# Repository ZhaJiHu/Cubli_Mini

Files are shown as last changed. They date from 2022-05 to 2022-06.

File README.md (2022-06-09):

# Cubli_Mini项目

本项目ID是来源于苏黎世联邦理工学院的Cubli，电机驱动使用的是Simple FOC。低成本、小型化、简化后作为我的首个开源项目

**项目完全开源，任何人都可以根据本Github内容自行白嫖，当然也可以顺手点个Star**

### 介绍

本项目在原版Cubli的基础上去掉主动刹车，缩小体积和一定的简化。需要手动调整到平衡点附近，才可以实现边和点平衡。Cubli_Mini是一个10x10x10CM的立方体，集电机驱动、充放电一体化。满电状态下，点平衡在无扰动下续航≥5小时。

项目成本：≤800RMB

**视频介绍：**[https://www.bilibili.com/video/BV1UR4y1c74B?spm_id_from=333.999.0.0](https://www.bilibili.com/video/BV1UR4y1c74B?spm_id_from=333.999.0.0)

YouTube：[https://youtu.be/JwiJBd6I_vY](https://youtu.be/JwiJBd6I_vY)

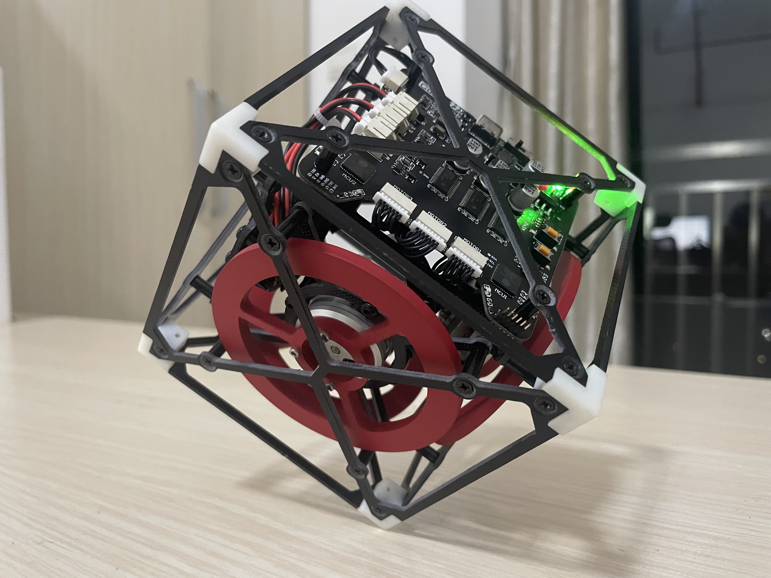
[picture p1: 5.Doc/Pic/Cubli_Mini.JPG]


### 资料更新说明（2022/6/7）

- **修复**：修复PCB BOM表采购链接的部分链接错误问题，**一共有4处，已经红色标红**。已经下单的同学需要自己校验看元器件是否是正确
- **增加**：PCB BOM表采购链接里的**贴片按键增加备用链接**

### 资料更新说明（2022/5/22）

- PCB BOM表添加采购链接
- 更新<写给小白的白嫖教程.pdf><代码和工程>，图文并茂说明如何解决头文件错误问题

### 资料更新说明（2022/5/21）c23

- /6.Process/钣金件/，增加对应的step文件
- /6.Process/3D打印/，增加对应的step文件
- **安全说明**
  - **动量轮比较危险，要注意安全，手远离动量轮**
  - /2.Firmware/MCU1/control/cubli_mini.h，修改VOLTAGE_LIMIT的电压可以限制飞轮的最大输出，开始使用建议降低该参数，可以从4，5V开始

### 资料更新说明（2022/5/19)

- 最新发现动量轮有两个角忘了倒角了，理论上会影响大转速下的动平衡，因此对此进行修改。已经下单打样的同学也可以正常使用，因为电机KV值很低，我现在使用的也是漏倒角的动量轮。更新了/4.Model/Cubli_Mini.STEP文件。并且更新了/6.Process/钣金件/YC.JGJ.000002.4.*，文件版本号更新到.4
- 还有说一下结构件的采购数量和采购链接都在/6.Process/BOM/结构BOM.xls
- 物料采购的时候注意编码器模块需要3套物料

### 资料说明

- 3D模型设计源文件
- 主控模块、IMU模块、编码器模块、下载模块硬件工程
- 主控1、主控2软件工程
    - 主控模块使用两颗ESP32
- 网络调试助手
    - WIFI调参使用
- 各类文档说明
    - 对项目的一些说明，如调参，按键操作，控制原理等
- 打样文件
    - STL格式3D打印文件
    - DWG格式钣金文件
    - BOM表
        - 结构BOM表
        - PCB元器件BOM表

### 结构设计

由于我只学了一周的SW，因此有些零件会漏画一些内容，如螺丝螺纹，铜柱内螺纹啥的

外框等钣金件采用的是成本较低的玻纤板，在保证刚性的情况下降低成本。动量轮采用的是304不锈钢，可以在小体积下提供较大的转动惯量。辅以少量3D打印件组成。连接件为了美观使用的是阳极氧化铝柱，当然也可以自行使用成本更低的铜柱。整体结构件成本为350块以内，铝柱更换铜柱可以降低到290以内

**注意事项：**

- Cubli_Mini的八个角点，是由两种不同的角组成，名字为角1和角2，各4个
- 外框和角的连接处的结构不是45°对称，所以是有安装方向的，详情看DoC/结构和安装说明

### 电路模块

**主控模块：**

- 主控模块集成了3个电机驱动电路，电池充放电路，降压稳压电路，CAN通讯电路
- 由于单颗ESP32只有6路电机PWM，因此使用了两颗ESP32模块，使用了CAN作为MCU间的通讯方式，由于两颗ESP32都是集成在同一个主板上，因此为了节省IC成本，可以把CAN修改为IIC，UART，SPI等各类短路径通讯方式，但是需要修改主控软硬件，有想法的同学可以自行修改
- 电机驱动电路参考Simple FOC开源电路，Simple FOC链接：[https://github.com/simplefoc](https://github.com/simplefoc)。电池充放电参考：[https://oshwhub.com/qqj1228/zi-ping-heng-di-lai-luo-san-jiao_10-10-ban-ben](https://oshwhub.com/muyan2020/zi-ping-heng-di-lai-luo-san-jiao_10-10-ban-ben_copy)

**IMU模块：**

- 使用最为常见的MPU6050
- 为了防止应力，对IMU所在区域挖槽，减少安装应力。但使用了3颗螺丝硬连接，并不能避免应力问题，改进方案为使用软垫片并只拧紧一个螺丝进一步减少应力
- 由于IMU安装要求比较高，因此在贴片时，尽量保证MPU6050与PCB平行，且位于焊盘正中央

**编码器模块：**

- 采用的是成本较低的AS5600，在低速情况下便宜好用

**自动下载模块：**

- 为了尽量减少主控的面积，因此单独把自动下载电路摘出来，参考官方自动下载电路

**注意事项：**

- 正常情况下，自动下载模块焊接排针，主控不焊接任何排针/排母

### 固件说明

Cubli_Mini的核心内容为Simple FOC电机驱动库以及点平衡控制算法，运行在MCU1中。MCU2只是使用了Simple FOC库对电机2和电机3的控制，利用CAN反馈和接收控制命令。

**MCU1固件说明：**

- bsp：基于arduino库封装了一下LED，KEY，ADC，非易失储存等内容
- comm：公用类，目前只封装了一个时间类，获取时间差，非延时等待等简单内容
- control：核心库，内容为平衡算法和调参接口，调参参考Simple FOC格式。为方便使用，使用的是字符串，不使用传统的16进制协议
- main：main文件，驱动的初始化和FreeRTOS任务创建
    - ESP32官方把WIFI，蓝牙类运行在Core0。因此在创建任务中，把WIFI任务创建在Core0中，其他则创建在Core1。只有运行于不同核心任务的数据交互我才加了互斥锁。

**注意事项：**

- 目前WIFI SSID和PSW，TCP Server IP Port全部是写死在固件里面，因此要想使用WIFI调参需要修改这些内容，详情请看Doc/使用和调参说明

### 打样说明

考虑到很多同学可能是第一次进行结构打样，因此提供了打样文件

**3D打印：**

- 文件位于：/6.Process/**3D打印**，该文件为STL格式，打样数量请查看同目录下的<**3D打印加工说明**>，可以在未来工厂或者嘉立创打样，首选光固化
- 文件名称使用的是料号，料号方便管理，尾号没有.X都代表为第一版

**钣金件打样：**

- 文件位于：/6.Process/**钣金件**，**每个物料的都有对应的PDF和DWG文件，PDF文件方便查看，DWG文件用于激光切割/板材加工**。打样数量请查看同目录下的<**钣金加工说明**>，可以找淘宝给图纸直接加工。由于加工精度要求不高，个人用途下，公差全看加工厂的心情
- 也可以直接找到对应的step文件给淘宝加工

**PCB打样：**

- 从硬件工程拿着PCB文件出门左转嘉立创白嫖

**BOM表：**

- 文件位于：/6.Process/**BOM**
- 结构BOM表，里面列有需要购买的**结构物料和链接**
- PCB BOM表，里面列有需要购买的元器件物料，也可以自行找到AD工程导出
- **注意事项：**
    - PCB BOM表是从AD源文件导出，工程会有重复用料，需要注意
    - **注意编码器需要3块，需要采购3套物料**
    - DRV8313、ESP32、AS5600、IMU可以去淘宝购买，其他右转立创商城BOM表下单。
    - **注意贴片型铝电解电容的封装，主控板有限高区域，限高高度为8mm**
    - 如文件有遗漏的地方望提醒

**写给小白的白嫖教程：**

- 文件位于：/Doc/写给小白的白嫖教程.pdf，手把手教你如何完成本项目的白嫖

### 控制算法

Cubli_Mini使用的是LQR来进行控制，也可以使用串级PID来进行控制。代码位于/需要修改/MCU1/control/cubli_mini

**边平衡**：

- 可以参考一阶倒立摆进行建模和求解参数。由于建立模型的参数比较难准确的获得，我求解得到的参数和最佳参数有些许出入。因此本项目大多数使用玄学调参工程师来整定参数

**点平衡：**

- 在边平衡的基础上添加对X，Z轴的控制。采用与边平衡一样的控制方法，详情看Doc/控制原理说明。

**研究型：**

- 请查看原版Cubli的论文

### 调参

**调节方法：**

- 可以使用UART和WIFI进行调参，WIFI需要连接到路由器，Cubli_Mini为TCP客户端

**调节命令：**

- 详情命令请查看Doc/调参命令说明

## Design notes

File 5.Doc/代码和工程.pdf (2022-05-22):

# 代码和⼯程

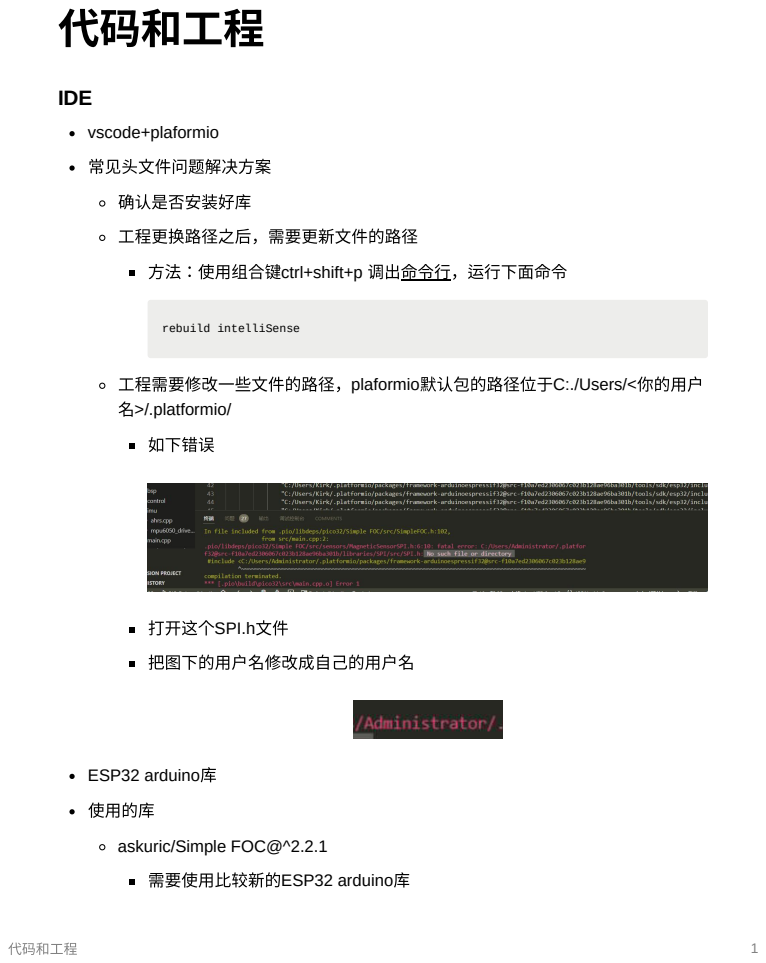
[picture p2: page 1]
代码和⼯程; IDE; vscode+plaformio; 常⻅头⽂件问题解决⽅案; 确认是否安装好库; rebuild intelliSense; 如下错误; 打开这个SPI.h⽂件; ESP32 arduino库

⼯程更换路径之后，需要更新⽂件的路径

⽅法：使⽤组合键ctrl+shift+p 调出命令⾏，运⾏下⾯命令 (https://so.csdn.net/so/search?q=%E5%91%BD%E4%BB%A4%E8%A1%8C&spm=1001.2101.3001.7020)

⼯程需要修改⼀些⽂件的路径，plaformio默认包的路径位于C:./Users/<你的⽤户
名>/.platformio/

把图下的⽤户名修改成⾃⼰的⽤户名

askuric/Simple FOC@^2.2.1
需要使⽤⽐较新的ESP32 arduino库

分⽀号为：6cfe4613e4b4846e1ab08c7f78b7ea241f52c7da

请查看⼯程⽬录下的plaformio.ini⽂件

miwagner/ESP32CAN@^0.0.1

### MCU1⽬录树

Mcu1
├─ .gitignore
├─ .vscode
│ ├─ extensions.json
│ └─ settings.json
├─ include
│ ├─ bsp 基于arduino库封装了⼀下
│ │ ├─ adc.h
│ │ ├─ bsp_driver.h
│ │ ├─ can.h
│ │ ├─ key.h
│ │ ├─ led.h
│ │ └─ my_eeprom.h
│ ├─ comm 公共类
│ │ └─ time.h
│ ├─ config 配置⽂件
│ │ └─ config.h
│ ├─ control 核⼼库，控制和调参
│ │ ├─ cubli_mini.h
│ │ ├─ param.h
│ │ ├─ serial_commander.h
│ │ └─ wifi_commander.h
│ ├─ imu IMU驱动和融合
│ │ ├─ ahrs.h
│ │ └─ mpu6050_driver.h
│ └─ README
├─ lib
│ └─ README
├─ platformio.ini
├─ README.md

├─ src
│ ├─ bsp
│ │ ├─ can.cpp
│ │ ├─ key.cpp
│ │ ├─ led.cpp
│ │ └─ my_eeprom.cpp
│ ├─ control
│ │ ├─ cubli_mini.cpp
│ │ ├─ param.cpp
│ │ ├─ serial_commander.cpp │ │ └─ wifi_commander.cpp
│ ├─ imu
│ │ ├─ ahrs.cpp
│ │ └─ mpu6050_driver.cpp
│ ├─ main.cpp
│ └─ workspace.code-workspace └─ test
└─ README

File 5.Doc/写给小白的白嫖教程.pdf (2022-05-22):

写给⼩⽩的⽩嫖教程 | 1

# 写给⼩⽩的⽩嫖教程

下载

1. clone或者Download整个项⽬

下单

1. PCB打样
a. 进⼊\1.Hardware\
b. 找到每⼀个硬件⼯程的PCB⽂件，直接右转丢到嘉⽴创打样
2. 开钢⽹
a. 把4个⼯程的PCB⽂件⼀起丢给淘宝，让淘宝开⼀张钢⽹就⾏
3. 下单3D打印件
a. 进⼊\6.Process\3D打印
b. 按照<3D打印加⼯说明.xlsx>⽂档说明，看清楚数量，去未来⼯⼚把3个物料丢上 去打印，材料选未来8100
4. 下单钣⾦件
a. 进⼊\6.Process\钣⾦件
b. 按照<钣⾦加⼯说明.xlsx>⽂档说明，看清楚数量，⾃⼰去淘宝打样或者找到 \6.Process\BOM\结构BOM.xls⽂件，点进去⽂件的链接，丢⽂件给客服，确定好 数量开⼯
5. 下单结构件
a. 进⼊\6.Process\BOM\
b. 按照<结构BOM.xls>下单除开钣⾦件的其他材料
6. 下单元器件
a. 进⼊进⼊\6.Process\BOM\
b. 按照<AS5600.xlsx><Cubli_Control_Board.xlsx><ESP32_UART.xlsx> <mpu6050.xlsx>⽂档下单元器件 i. 嫌⿇烦，有钞能⼒的除开AS5600去淘宝，其他全去⽴创商城BOM表下单， 需要注意贴⽚型铝电解电容的封装，主控板有限⾼区域，限⾼⾼度为8mm

ii. 淘宝IC⽔深，注意别翻⻋了

iii. 贴出了元器件链接

### 安装IDE和编译

1. 等物料的过程可以在PC装好Vscode+plaformio环境
a. 请去百度或者B站搜索相关教程
2. 编译\2.Firmware⾥MCU1、MCU2的代码，编译有些问题可以查看\5.Doc\代码和⼯ 程.pdf，有其他问题可以百度解决

## PCB焊接

1. 先焊接PCB
a. 可以看看视频⽅法，没有加热台⽤热⻛枪吹
b. 注意：要注意IMU模块的⽴贴接插件，引脚是否焊接到PCB上，这⾥经常翻⻋
2. 焊接完PCB⼀定要测试⼀下
a. 把所有的模块接上线
b. ⽤万⽤表打到⼆极管档位或者通断档位
c. 分别测量VBUS\BAT+\12V\5V\3.3V与GND的测试点，看是否有短路，⽆异常就 可以了
3. 把电机和编码器部分先装配好
a. 作⽤：为了测试功能
4. 上电测试主控、IMU、电机、下载模块
a. 线都接好了，就可以上电了下载代码了，给2个MCU都下载代码，注意MCU编 号，⽤串⼝助⼿查看是否所有模块都正常初始化？
b. 电池⼀定要注意线序
c. 初始化通过后，按3次KEY2切换到电机测试模式，⻓按KEY1，正常的话3个电机 都能正常运⾏。模式和状态指⽰灯请查看<模式以及切换（KEY）说明.pdf><LED 指⽰灯说明.pdf>

装配

1. 确保硬件都没问题了，就可以开始装配了，装配没啥难度，按照\4.Model\⾥⾯的⽂件 或者视频装配就可以了，就是需要注意⼀下
a. ⾓和外框装配有⽅向，可以看<结构和安装说明>
b. 电机CH1、CH2、CH3也按照<结构和安装说明>来接线
2. 都装配完成就可以开始正常上机了
a. 按⼀次KEY2切换到点平衡模式，绿⾊LED3S内闪烁⼀次
b. ⼿动把Cubli_Mini⽴起来放到平衡点附近，静⽌0.5S就可以正常运⾏了，本步骤 只是确保系统和传感器都能正常运⾏
c. 未调整平衡⾓度有⼀定的概率能⽴起来
d. 注意事项
i. ⼀定⼀定要注意安全，⼿要远离动量轮

ii. ⼀开始⼀定要调低输出的电压阈值，调整⽅法
为：/2.Firmware/MCU1/control/cubli_mini.h，修改VOLTAGE_LIMIT的电压 可以限制⻜轮的最⼤输出，开始使⽤建议降低该参数，可以从4，5V开始

调参

1. 按照<使⽤和调参说明.pdf>使⽤串⼝或者WIFI调参
2. 按照<常⻅问题.pdf>第五点调节平衡⾓度，调节的命令查看<调参命令说明.pdf>

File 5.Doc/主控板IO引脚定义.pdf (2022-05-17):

主控板IO引脚定义 | 1

# 主控板IO引脚定义

# MCU1

类型 | 作⽤ | 引脚定义
MOTOR1 | PWM1 | IO25
| PWM2 | IO26
| PWM3 | IO27
| PWM_EN | IO33
| SCL | IO14
| SDA | IO4
CAN1 | CAN_TXD | IO15
| CAN_RXD | IO13
LED | LED_BLUE | IO10
| LED_GREEN | IO9
| LED_MOTOR_GREEN | IO21
ADC | BAT_V | IO36
IMU | SCL | IO18
| SDA | IO5
| INTERRUPT | IO23
KEY | KEY1 | IO22
| KEY2 | IO19

# MCU2

类型 | 作⽤ | 引脚定义
MOTOR2 | PWM1 | IO25
| PWM2 | IO26
| PWM3 | IO27
| PWM_EN | IO33

主控板IO引脚定义 | 2
类型 | 作⽤ | 引脚定义
| SCL | IO14
| SDA | IO4
MOTOR3 | PWM1 | IO22
| PWM2 | IO19
| PWM3 | IO23
| PWM_EN | IO21
| SCL | IO18
| SDA | IO5
LED | LED_MOTOR_GREEN | IO10
CAN2 | CAN2_TXD | IO15
| CAN2_RXD | IO13

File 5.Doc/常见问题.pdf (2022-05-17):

常⻅问题 | 1

# 常⻅问题

1. 为什么系统上电初始化需要静置?
a. 原因：IMU零偏问题，IMU需要连续1.5S的时间采集陀螺仪的数据做为零偏，静 置的条件默认需要三轴陀螺仪的读数＜5deg/s（默认，可以在 include/config/config.h中修改阈值），如果IMU的零偏值过⼤，建议更换零偏值 较⼩的IMU
2. 为什么我的IMU模块零偏特别⼤？
a. 安装应⼒，虽然IMU模块把IMU单独挖出来，但是因为上了3颗螺丝，IMU仍然有 可能会受到应⼒的变化，这时候可以通过添加软垫⽚的⽅法解决⼀部分，螺丝尽 量别打太紧，把IMU固定即可
b. IMU IC（mpu6050）原因，IC由于是mems传感器，可能会由于跌落等原因导致 IMU的物理结构受到影响，因⽽导致零偏过⼤，零偏过⼤，不建议使⽤
3. 为什么每个cubli都需要校准平衡的⾓度偏差值？
a. IMU安装之后的轴偏差问题，只讨论轴的所在平⾯是否垂直，不讨论原点是否重 合平⾯的问题
i. 单边平衡问题，结构设计上，处于平衡状态时，IMU反馈的⾓度理论上应该 为0。但是由于⽀点也好，IMU安装件也好都由于误差，会导致在平衡状态 时，IMU的读数不为0，因此需要校准⾓度偏差值

ii. 单点平衡问题同理

4. 为什么我明明已经调参到最佳平衡点了，每次重新上电后总是会发⽣变化，系统不处 于我上次调整的状态？
a. IMU的零偏问题，由于每次IMU上电后零偏会发⽣变化，带来的是融合结果发⽣ 变化，因此体现在动态⾓度上会有些许变化，导致平衡点产⽣偏移，因此上次校 准值不再为最佳参数
b. 解决⽅法
i. 更换性能更好的IMU模块

ii. 采⽤性能更好的IMU融合算法

iii. 对IMU的加速度计和陀螺仪都进⾏校准

常⻅问题 | 2
5. 怎么调整平衡点？
a. 单边情况下，观察动量轮的转动⽅向和转动速度，转动⽅向是与⽅块倾斜⽅向⼀ 致，平衡⾓的偏差⼤⼩决定系统需要的转动惯量，如转动⽅向为顺时针，那么⽅ 块⼀定是往右倾斜，因此需要往反⽅向调节平衡⾓度，调整到动量轮速度⼏乎为 0，这时候就为最佳平衡点
b. 单点情况下，X\Y轴哪个轴倾斜⼤调哪个，调节⽅法同单边
6. 为什么按照默认参数不能⽴起来？
a. 在系统中，控制⾓度θ越⼤，需要的转动惯量也就越⼤。想要更⼤的转动惯量， 要么提⾼动量轮的质量，要么提⾼动量轮的转速。因为所⽤的动量轮质量是恒定 的，所以只能提⾼动量轮的转速。由于所选电机的转速较低，因此很容易达到电 机最⼤转速，失去调节效果，所以⽴⽅体就⽆法再保持平衡。因此需要调整theta ⾓，使得⽴⽅体在转速范围内能提供⾜够的转动惯量去维持⽴⽅体的平衡。

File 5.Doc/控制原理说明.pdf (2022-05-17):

# 控制原理说明

## 单边平衡

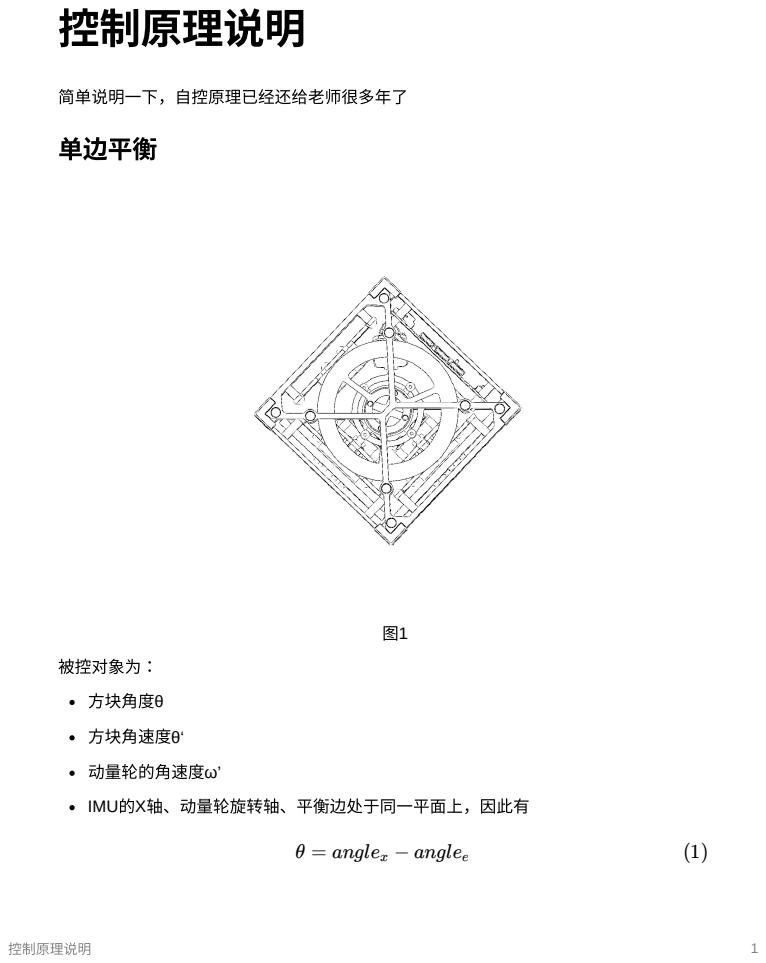
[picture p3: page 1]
控制原理说明; 被控对象为：; ⽅块⾓速度θ‘; 动量轮的⾓速度ω’; θ = anglex − anglee

简单说明⼀下，⾃控原理已经还给⽼师很多年了

IMU的X轴、动量轮旋转轴、平衡边处于同⼀平⾯上，因此有

结合（1）（2）（3）可得

### 参数整定

参数 | 默认数值（默认不 改结构件） | 说明
Kp | -25
Kv | 2
Ks | 0.5
angle_e | 0 | IMU安装误差

## 单点平衡

控制原理为在单边平衡的基础上增加对Y、Z轴的控制

结构如图2所⽰

θ =

′ | gyrox | (2)
ω’ = motorspeedx | (3)
Lqr = (anglex − anglee ) × kp + gyrox × kv + motorspeedx × ks | (4)

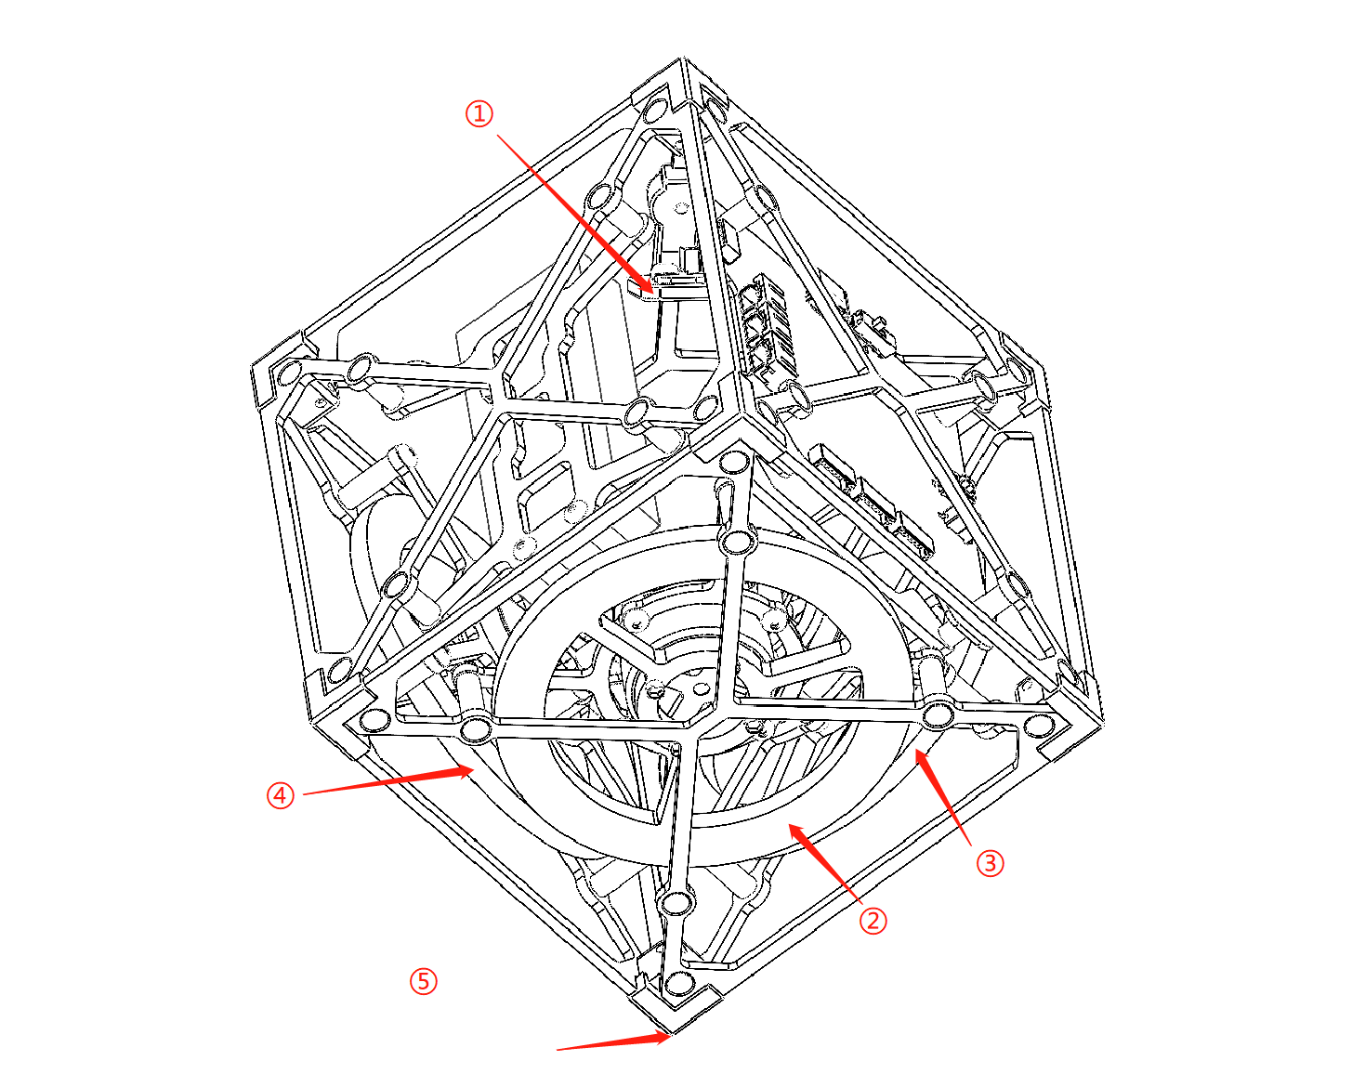
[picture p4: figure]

图2

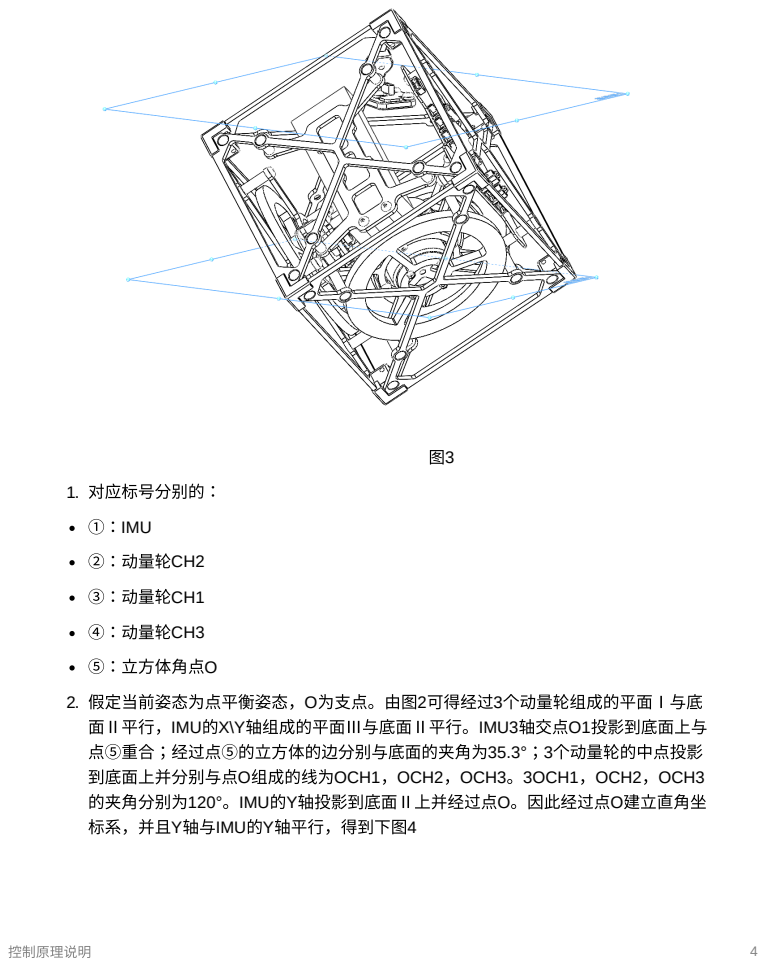
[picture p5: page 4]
1. 对应标号分别的：; ①：IMU; ②：动量轮CH2; ③：动量轮CH1; ④：动量轮CH3

2. 假定当前姿态为点平衡姿态，O为⽀点。由图2可得经过3个动量轮组成的平⾯Ⅰ与底
⾯Ⅱ平⾏，IMU的X\Y轴组成的平⾯Ⅲ与底⾯Ⅱ平⾏。IMU3轴交点O1投影到底⾯上与
点⑤重合；经过点⑤的⽴⽅体的边分别与底⾯的夹⾓为35.3°；3个动量轮的中点投影
到底⾯上并分别与点O组成的线为OCH1，OCH2，OCH3。3OCH1，OCH2，OCH3
的夹⾓分别为120°。IMU的Y轴投影到底⾯Ⅱ上并经过点O。因此经过点O建⽴直⾓坐
标系，并且Y轴与IMU的Y轴平⾏，得到下图4

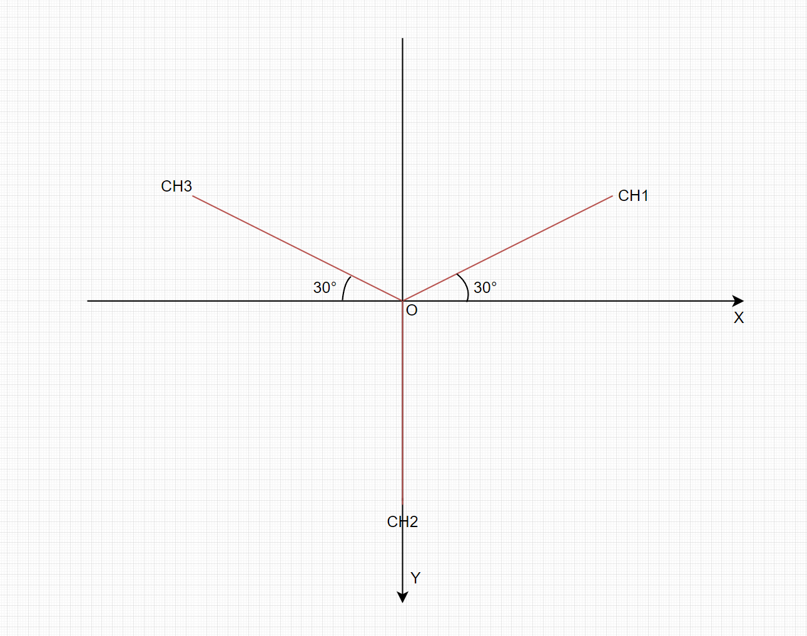
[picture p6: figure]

图4

3. 动量轮CH1\CH2\CH3的转动速度⽅向与OCH1\OCH2\OCH3垂直，因此分别平⾏移 动到经过点0后可以得到下图

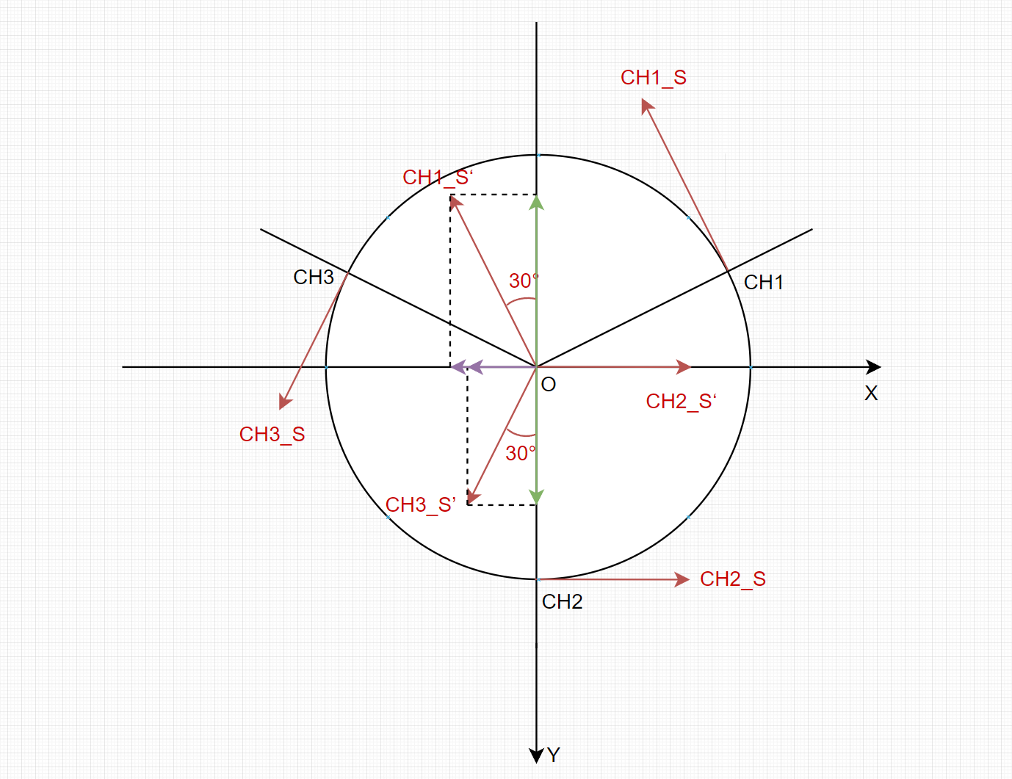
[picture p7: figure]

图5

由图5的关系可以得到（4）（5）（6）

根据单边控制⽅法分别控制X，Y，Z轴，可得（7）（8）（9）

sx = sch2 − sch1 × sin(30°) − sch3 × sin(30°) | (4)
sy = sch3 × cos(30°) − sch1 × cos(30°) | (5)
sz = sch1 + sch2 + sch3 | (6)
Lx = (anglex − anglexe ) × kxp + gyrox × kxv + sx × kxs | (7)
Ly = (angley − angleye ) × kyp + gyroy × kyv + sy × kys | (8)
Lz = (anglez − angleye ) × kzp + gyroz × kzv + sz × kzs | (9)

由图6可得（10）（11）（12）

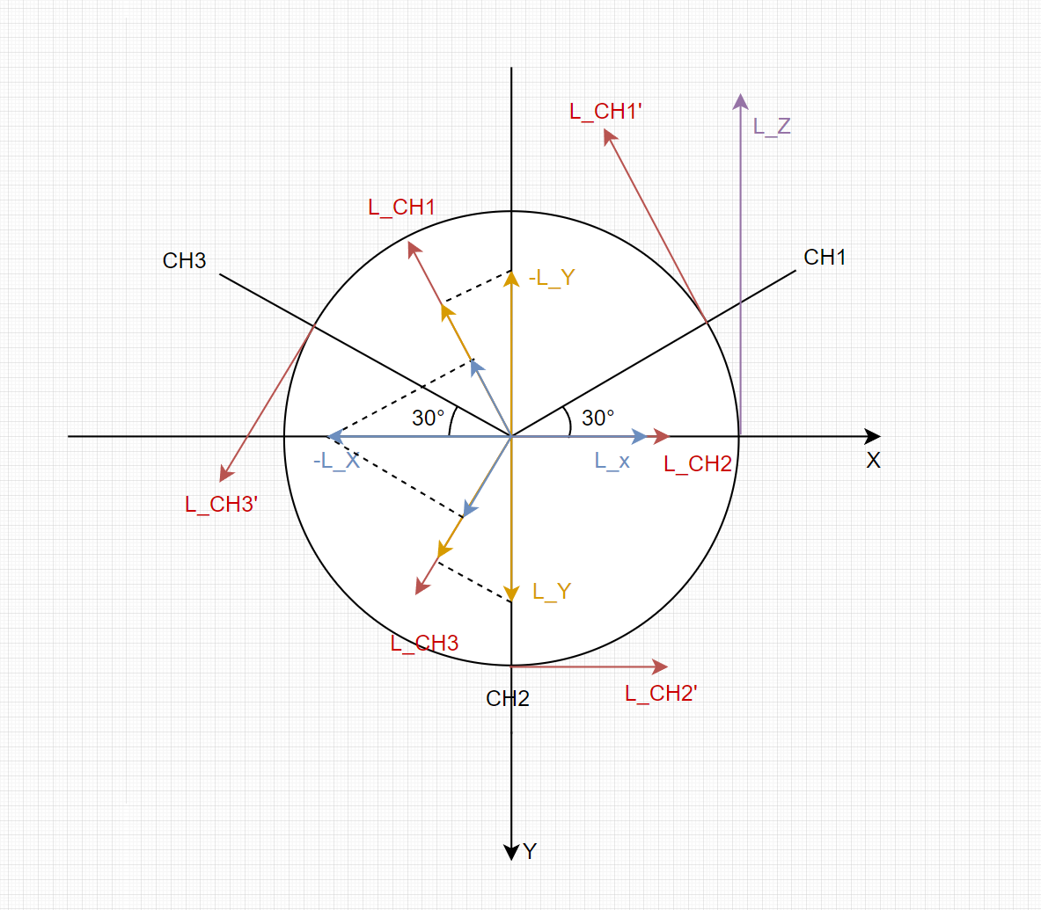
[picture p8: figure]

图6

### 参数整定

## Sch1 = −Ly × cos(30°) − Lx × sin(30°) +

3

Lz
(10)

Sch2 = Lx +
3

Lz
(11)

## Sch3 = Ly × cos(30°) − Lx × sin(30°) +

3

Lz
(12)

参数 参数 | 默认数值（默认 默认数值（默认 不改结构，⽞学 不改结构，⽞学 调参） 调参） | 说明 说明
Kxp | -17
Kxv | 1.5
Kxs | 0.3
angle_xe | 0.5 | IMU安装误差
Kyp | 18
Kyv | 1.6
Kys | 0.3
angle_ye | 1.5
Kzp | 0 | IMU安装误差
Kzv | -0.3
Kzs | 0.02
angle_ze | 0 | 默认不对Z轴⾓度控制，IMU 的Z轴会因为零偏漂移

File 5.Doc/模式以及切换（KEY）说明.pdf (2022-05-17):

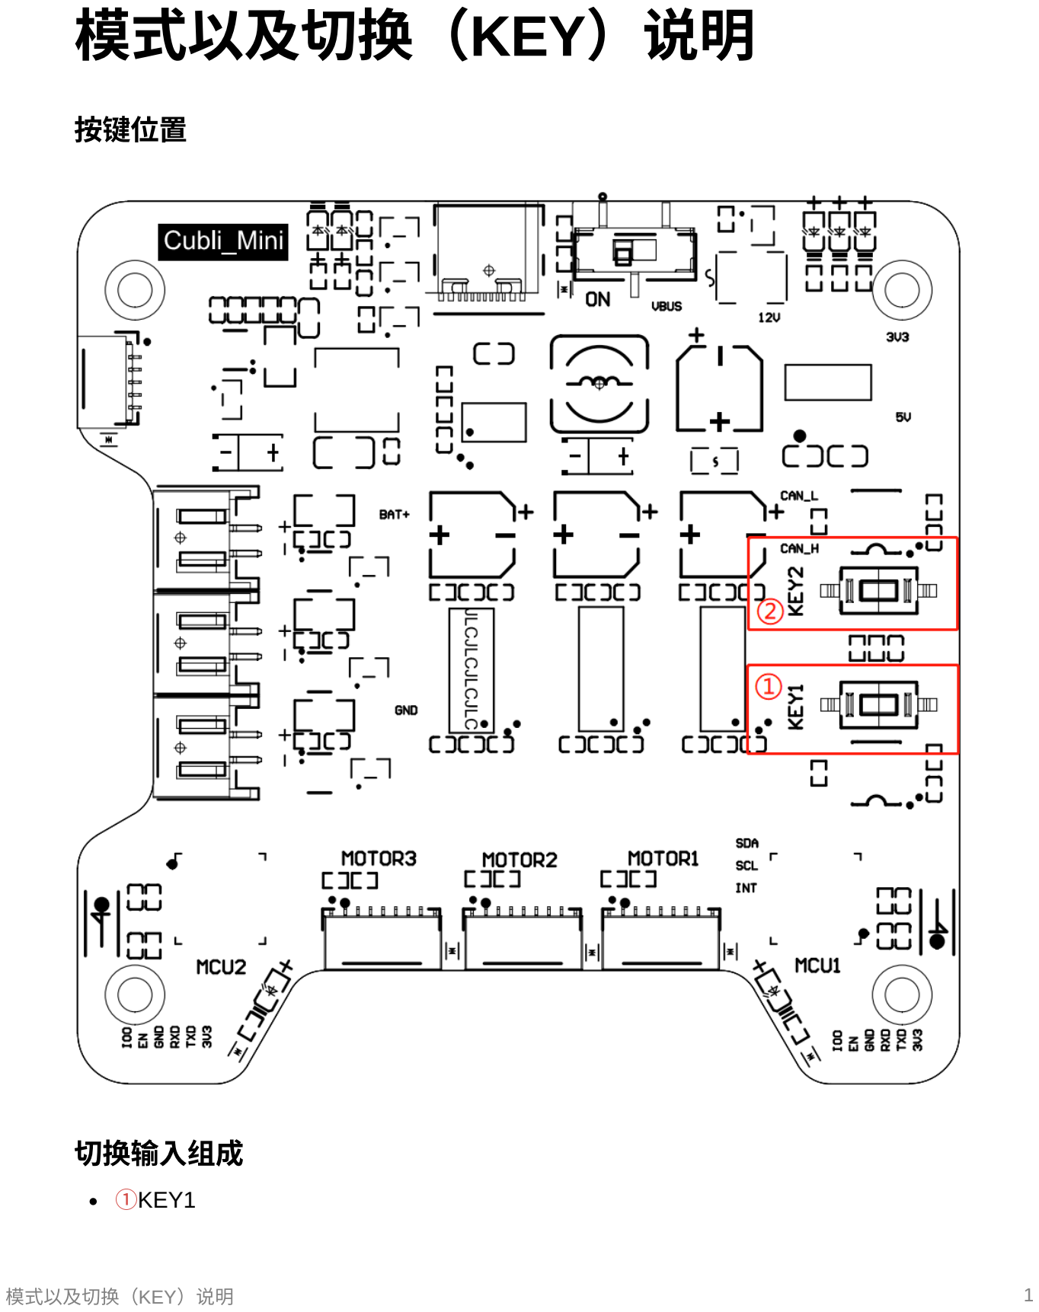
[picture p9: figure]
模式以及切换（KEY）说明; 按键位置; 切换输⼊组成; ①KEY1

### ②KEY2

## KEY作⽤

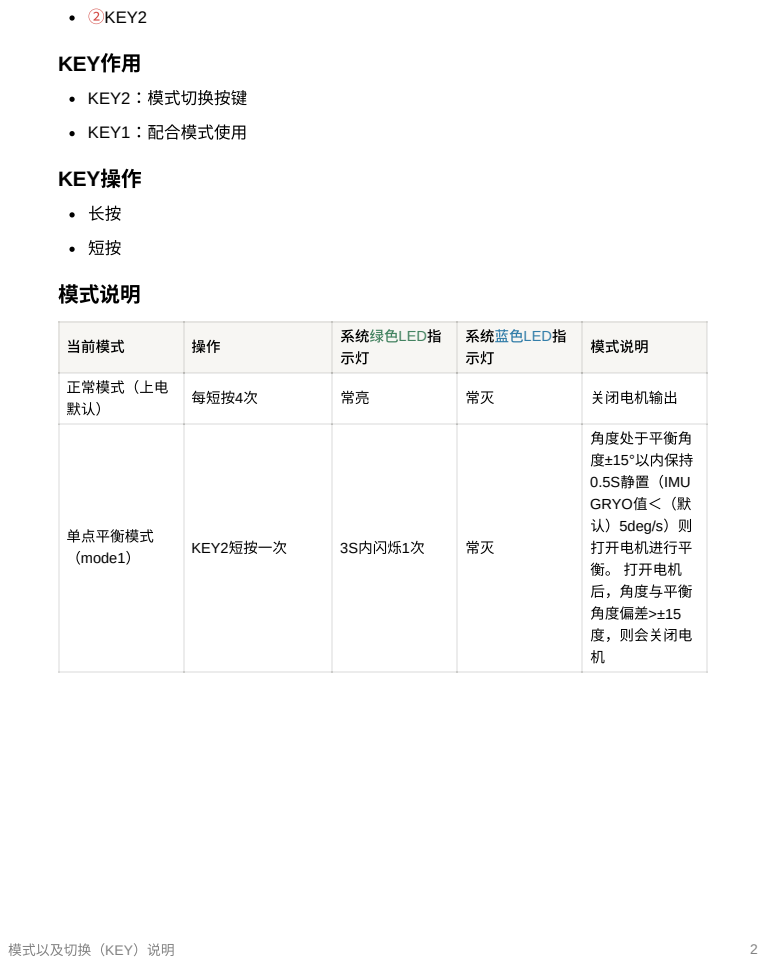
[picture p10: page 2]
KEY2：模式切换按键; KEY1：配合模式使⽤; KEY操作; 模式说明

当前模式 | 操作 | 系统绿⾊LED指 ⽰灯 | 系统蓝⾊LED指 ⽰灯 | 模式说明

正常模式（上电 默认） | 每短按4次 | 常亮 | 常灭 | 关闭电机输出

单点平衡模式 （mode1） | KEY2短按⼀次 | 3S内闪烁1次 | 常灭 | ⾓度处于平衡⾓ 度±15°以内保持 0.5S静置（IMU GRYO值＜（默 认）5deg/s）则 打开电机进⾏平 衡。 打开电机 后，⾓度与平衡 ⾓度偏差>±15 度，则会关闭电 机

当前模式 | 操作 | 系统绿⾊LED指 ⽰灯 | 系统蓝⾊LED指 ⽰灯 | 模式说明
单边平衡模式 （mode2） | KEY2短按两次 | 3S内闪烁2次 | 常灭 | ⾓度处于平衡⾓ 度±15°以内保持 0.5S静置（IMU GRYO值＜（默 认）5deg/s）则 打开电机进⾏平 衡。 打开电机 后，⾓度与平衡 ⾓度偏差>±15 度，则会关闭电 机
电机测试模式 （mode3） | KEY2短按三次 | 3S内闪烁3次 | 常灭 | 测试板⼦使⽤， 看电机是否正常 运⾏
单点平衡⾓度校 准模式 （mode4） | mode1下 1. ⻓按 KEY1进⼊校准模 式，校准结束后进⼊ 正常模式 2. 进⼊校 准模式后，再次⻓按 KEY1则退出校准模 式，进⼊正常模式 | 3S内闪烁1次 | 快速闪烁 | ⾓度处于平衡⾓ 度±15°以内保持 0.5S静置（IMU GRYO值＜（默 认）5deg/s）则 开始校准⾓度
单边平衡⾓度校 准模式 （mode5） | mode2下 1. ⻓按 KEY1进⼊校准模 式，校准结束后进⼊ 正常模式 2. 进⼊校 准模式后，再次⻓按 KEY1则退出校准模 式，进⼊正常模式 | 3S内闪烁2次 | 快速闪烁 | ⾓度处于平衡⾓ 度±15°以内保持 0.5S静置（IMU GRYO值＜（默 认）5deg/s）则 开始校准⾓度
电机测试模式开 启测试模式 （mode6） | mode3下 1. ⻓按 KEY1开启电机，默 认给0.5V电压 2. ⽆ 退出操作，只能切换 模式 | 3S内闪烁3次 | 快速闪烁 | 测试板⼦使⽤， 看电机是否正常 运⾏
低电量 | 系统电压低于10V | 任意状态 | 常亮 | 关闭电机输出

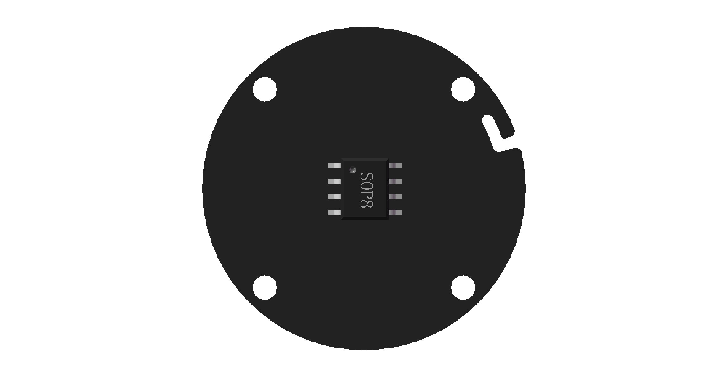
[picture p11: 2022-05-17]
5.Doc/Pic/AS5600_B.PNG

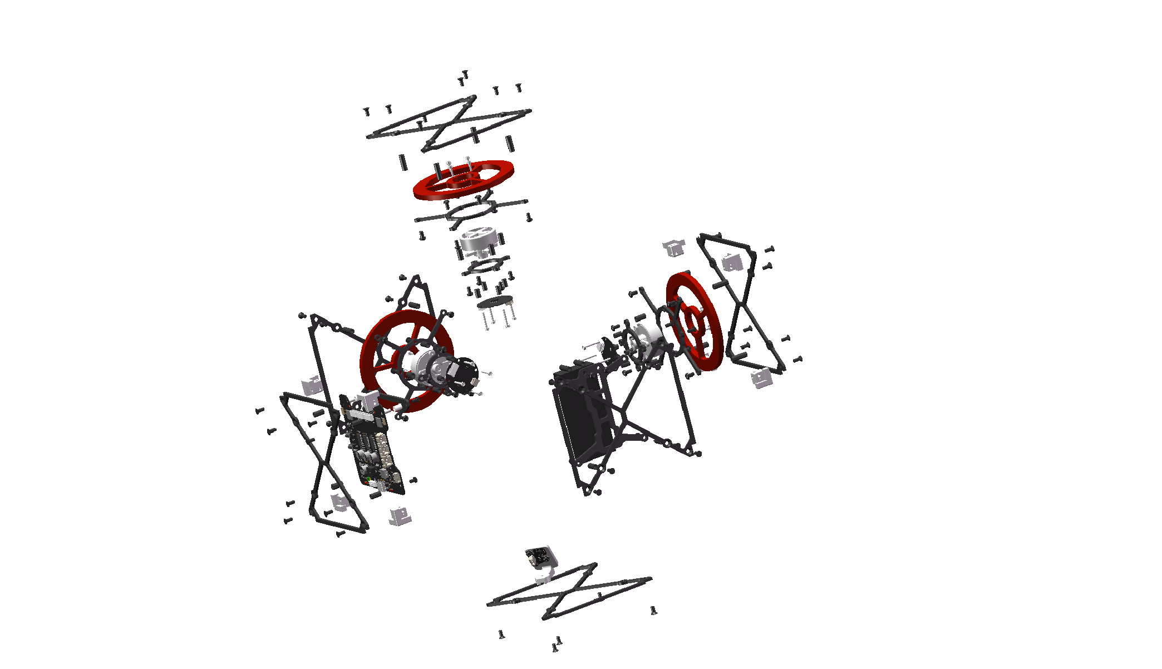
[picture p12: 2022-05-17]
5.Doc/Pic/爆炸图.PNG

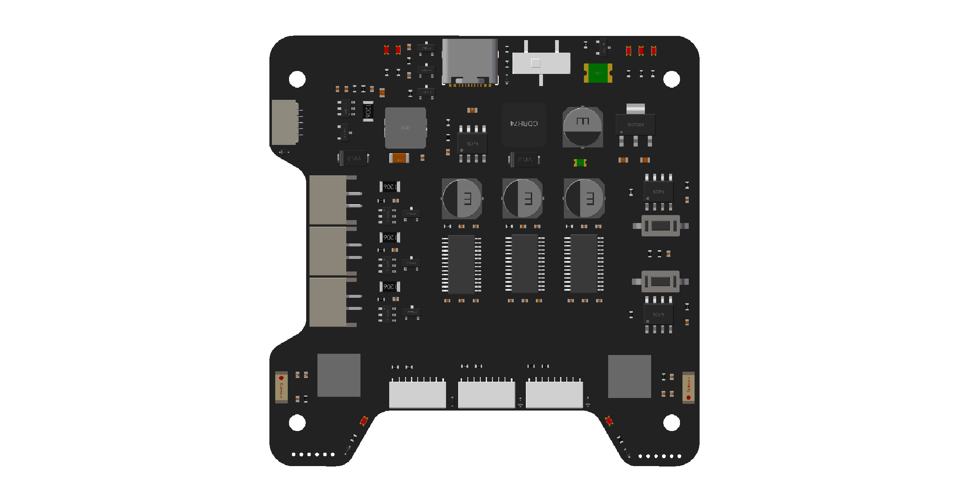
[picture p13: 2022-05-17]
5.Doc/Pic/Cubli_Control_Board.PNG

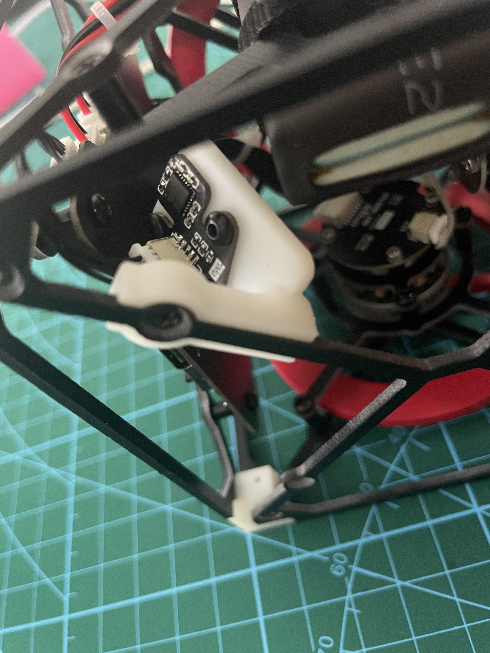
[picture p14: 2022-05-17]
5.Doc/Pic/IMU.JPG

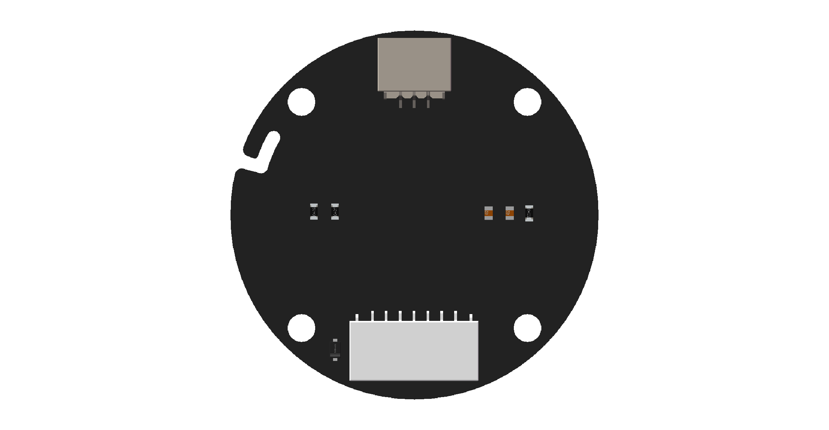
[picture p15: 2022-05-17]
5.Doc/Pic/AS5600.PNG

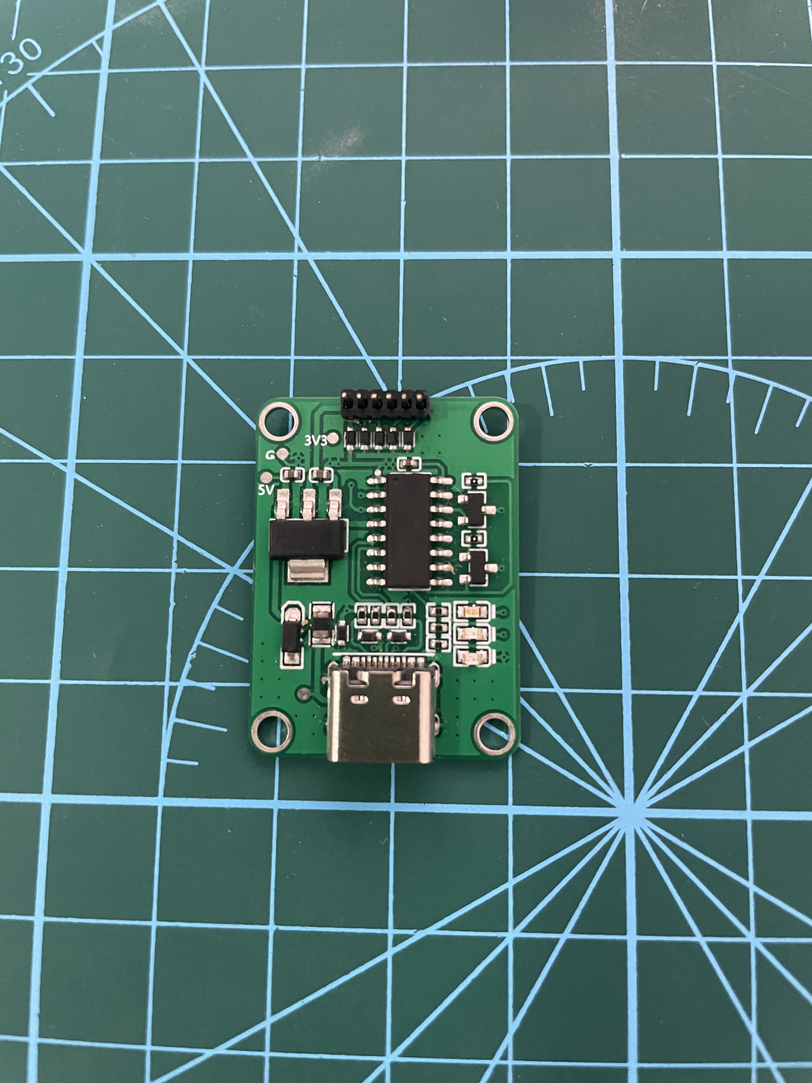
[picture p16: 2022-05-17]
5.Doc/Pic/ESP32_UART.JPG

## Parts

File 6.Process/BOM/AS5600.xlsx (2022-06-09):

Comment | Description | Designator | Footprint | LibRef | Quantity | 途径 | 链接
10uF (106) 20% 6.3V | 贴片电容 | C1 | 0402_C | 0402 10uF (106) 20% 6.3V | 1 | 立创商场 | https://item.szlcsc.com/16204.html
100nF (104) 10% 16V | 贴片电容 | C2 | 0402_C | 0402 100nF (104) 10% 16V | 1 | 立创商场 | https://item.szlcsc.com/107097.html
HC-1.0-3PWT |  | CN1 | CONN-SMD_3P-P1.0-HC-1.0-3PWT | HC-1.0-3PWT | 1 | 立创商场 | https://item.szlcsc.com/3039043.html
HC-1.0-7PWT |  | CN2 | CONN-SMD_HC-1.0-7PWT | HC-1.0-7PWT | 1 | 立创商场 | https://item.szlcsc.com/3039047.html
ESD5Z3.3C |  | D1 | SOD-523_L1.2-W0.8-LS1.6-BI | ESD5Z3.3C | 1 | 立创商场 | https://item.szlcsc.com/515057.html
0Ω (0R0) ±1% | 贴片电阻 | R1 | 0402_R | 0402 0Ω (0R0) 1% | 1 | 立创商场 | https://item.szlcsc.com/308197.html
4.7KΩ (4701) ±1% | 贴片电阻 | R2, R3 | 0402_R | 0402 4.7KΩ (4701) 1% | 2 | 立创商场 | https://item.szlcsc.com/26643.html
AS5600-ASOT |  | U1 | SOIC-8_L5.0-W4.0-P1.27-LS6.0-BL | AS5600-ASOT | 1 | 淘宝 | https://item.taobao.com/item.htm?spm=a1z09.2.0.0.29a92e8db59EqX&id=633037124155&_u=m1jbj7pb2330

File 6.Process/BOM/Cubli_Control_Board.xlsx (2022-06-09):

Comment | Description | Designator | Footprint | LibRef | Quantity | 途径 | 链接 | 备用选项
100nF (104) 10% 16V | 贴片电容 | C1, C2, C7, C11, C13, C16, C17, C18, C21, C22, C26, C27, C29, C32, C33, C35, C38, C39, C41 | 0402_C | 0402 100nF (104) 10% 16V | 19 | 立创商城 | https://item.szlcsc.com/107097.html
22uF ±20% 25V | 贴片电容 | C8 | 1206_C | 1206 1uF (105) 10% 50V | 1 | 立创商城 | https://item.szlcsc.com/360044.html
10uF ±10% 25V | 贴片电容 | C9 | 0603_C | 0603 10uF (106) 10% 10V | 1 | 立创商城 | https://item.szlcsc.com/3232963.html
100nF ±10% 50V | 贴片电容 | C10 | 0402_C | 0402 100nF (104) 10% 16V | 1 | 立创商城 | https://item.szlcsc.com/107097.html
4.7uF ±20% 16V | 贴片电容 | C12 | 0402_C | 0402 4.7uF (475) 20% 10V | 1 | 立创商城 | https://item.szlcsc.com/299692.html
1.0uF (105) 10% 25V | 贴片电容 | C14, C15, C20, C24 | 0402_C | 0402 1.0uF (105) 10% 25V | 4 | 立创商城 | https://item.szlcsc.com/1054203.html
10uF (106) 20% 6.3V | 贴片电容 | C19, C23, C30, C36, C42 | 0402_C | 0402 10uF (106) 20% 6.3V | 5 | 立创商城 | https://item.szlcsc.com/16204.html
10nF (103) 10% 50V | 贴片电容 | C25, C31, C37, C43 | 0402_C | 0402 10nF (103) 10% 50V | 4 | 立创商城 | https://item.szlcsc.com/77832.html
100uF 35V | 5*12.5*20 | C28, C34, C40 | CAP-SMD_L6.6-W6.6 | C | 3 | 立创商城 | https://item.szlcsc.com/3002614.html
10uF ±20% 25V | 贴片电容 | C44, C46, C47 | 0603_C | 0603 10uF (106) 10% 10V | 3 | 立创商城 | https://item.szlcsc.com/3232963.html
220uF 25V | 5*12.5*20 | C45 | CAP-SMD_L6.6-W6.6 | C | 1 | 立创商城 | https://item.szlcsc.com/729802.html
HC-1.0-7PWT |  | CN1, CN2, CN3 | CONN-SMD_HC-1.0-7PWT | HC-1.0-7PWT | 3 | 立创商城 | https://item.szlcsc.com/3039047.html
HC-1.0-5PWT |  | CN4 | CONN-SMD_5P-P1.00_HCTL_HC-1.0-5PWT | HC-1.0-5PWT | 1 | 立创商城 | https://item.szlcsc.com/3039045.html
ESD5Z3.3C |  | D1, D2, D3, D4, D8, D12 | SOD-523_L1.2-W0.8-LS1.6-BI | ESD5Z3.3C | 6 | 立创商城 | https://item.szlcsc.com/3261722.html
SS34K |  | D4, D14 | SMA_L4.3-W2.6-LS5.2-RD | SS34K | 2 | 立创商城 | https://item.szlcsc.com/3119637.html
红灯 0603 | 发光二极管 | D5, D15 | 0603_LED_S1 | 0603 红灯 | 2 | 立创商城 | https://item.szlcsc.com/85432.html
绿灯 0603 | 发光二极管 | D6, D10, D11, D13 | 0603_LED_S1 | 0603 绿灯 | 4 | 立创商城 | https://item.szlcsc.com/85436.html
LESD5D5.0CT1G |  | D7 | SOD-523_L1.2-W0.8-LS1.6-BI | LESD5D5.0CT1G | 1 | 立创商城 | https://item.szlcsc.com/356518.html
蓝灯 0603 | 发光二极管 | D9 | 0603_LED_S1 | 0603 蓝灯 | 1 | 立创商城 | https://item.szlcsc.com/85435.html
MF-MSMF250/16X-2 |  | F1 | F1812 | JK | 1 | 立创商城 | https://item.szlcsc.com/211716.html
JK-SMD0805-300L |  | F2 | F0805 | JK | 1 | 立创商城 | https://item.szlcsc.com/3034451.html
33uH ±20% 2A |  | L1 | IND-SMD_L7.1-W6.6 | L | 1 | 立创商城 | https://item.szlcsc.com/160911.html
AN2051-245 |  | L2, L3 | ANT2051 | AN2051-245 | 2 | 淘宝 | https://item.taobao.com/item.htm?spm=a1z09.2.0.0.40582e8dWqLc0W&id=558699169012&_u=m1jbj7pb6d0d
22uH ±20% 3A |  | L4 | CDRH74 | L | 1 | 立创商城 | https://item.szlcsc.com/760391.html
HDR1.27-LI-6P |  | P1, P2 | HDR1.27-LI-6P | HDR1.27-LI-6P | 2 | 立创商城 | https://item.szlcsc.com/3809.html
PH2.0-WS-2P |  | PH1, PH2, PH3 | PH2.0-WS-2P | PH2.0-WS-2P | 3 | 立创商城 | https://item.szlcsc.com/698563.html
AO3400A_C700953 |  | Q1 | SOT-23-3_L2.9-W1.3-P1.90-LS2.4-BR | AO3400A_C700953 | 1 | 立创商城 | https://item.szlcsc.com/736021.html
AP2300 |  | Q2, Q3, Q8 | SOT-23-3_L2.9-W1.3-P0.95-LS2.4-BR | AP2300 | 3 | 立创商城 | https://item.szlcsc.com/335325.html
SS8050 |  | Q4, Q5, Q6 | SOT-23-3_L2.9-W1.3-P1.90-LS2.4-BR | SS8050 | 3 | 立创商城 | https://item.szlcsc.com/192557.html
AP2335 |  | Q7 | SOT-23-3_L2.9-W1.6-P1.90-LS2.8-BR | AP2335 | 1 | 立创商城 | https://item.szlcsc.com/2976808.html
0Ω (0R0) ±1% | 贴片电阻 | R1, R3 | 0402_R | 0402 0Ω (0R0) 1% | 2 | 立创商城 | https://item.szlcsc.com/305682.html
120Ω (1200) ±1% | 贴片电阻 | R2, R4 | 0402_R | 0402 120Ω (1200) 1% | 2 | 立创商城 | https://item.szlcsc.com/293680.html
56Ω ±1% | 贴片电阻 | R5, R6, R7, R8, R9, R10 | 0402_R | 0402 56KΩ (5602) 1% | 6 | 立创商城 | https://item.szlcsc.com/25870.html
100Ω ±1% | 贴片电阻 | R15, R21, R26 | 1206_R | 1206 22Ω (22R0) 1% | 3 | 立创商城 | https://item.szlcsc.com/18589.html
19.1kΩ ±1% | 贴片电阻 | R16 | 0402_R | 0402 1KΩ (1001) 1% | 1 | 立创商城 | https://item.szlcsc.com/53049.html
0.1Ω (R100) ±1% | 贴片电阻 | R17 | 1206_R | 1206 0.1Ω (R100) 1% | 1 | 立创商城 | https://item.szlcsc.com/199477.html
1KΩ (1001) ±1% | 贴片电阻 | R18, R20, R22, R24, R27, R32, R33, R34, R38, R44 | 0402_R | 0402 1KΩ (1001) 1% | 10 | 立创商城 | https://item.szlcsc.com/226431.html
2KΩ (2001) ±1% | 贴片电阻 | R19 | 0402_R | 0402 2KΩ (2001) 1% | 1 | 立创商城 | https://item.szlcsc.com/288650.html
22KΩ (2202) ±1% | 贴片电阻 | R23, R25 | 0402_R | 0402 22KΩ (2202) 1% | 2 | 立创商城 | https://item.szlcsc.com/251122.html
5.1KΩ (5101) ±1% | 贴片电阻 | R28, R29 | 0402_R | 0402 5.1KΩ (5101) 1% | 2 | 立创商城 | https://item.szlcsc.com/279163.html
10KΩ (1002) ±1% | 贴片电阻 | R30, R31, R36, R37, R39, R40, R41, R42 | 0402_R | 0402 10KΩ (1002) 1% | 8 | 立创商城 | https://item.szlcsc.com/251116.html
42.2kΩ ±0.5% | 贴片电阻 | R35 | 0402_R | 0402 1KΩ (1001) 1% | 1 | 立创商城 | https://item.szlcsc.com/302407.html
3.3KΩ (3301) ±1% | 贴片电阻 | R43 | 0402_R | 0402 3.3KΩ (3301) 1% | 1 | 立创商城 | https://item.szlcsc.com/3186280.html
LSSAM12-V-T/R |  | SW1 | SW-SMD_LSSAM12-V-T-R | LSSAM12-V-T/R | 1 | 立创商城 | https://item.szlcsc.com/507364.html
DTSML-31S-V-T/R |  | SW2, SW3 | SW-SMD_L6.0-W3.5-LS9.0-1 | DTSML-31S-V-T/R | 2 | 立创商城 | https://item.szlcsc.com/507328.html | https://item.szlcsc.com/300341.html
TP |  | TP1, TP2, TP3, TP4, TP5, TP6, TP8, TP10, TP18, TP19, TP20 | TP_1X1MM | TP | 11 | 立创商城 | 不需要
TJA1040T/CM,118 |  | U1, U2 | SOIC-8_L5.0-W4.0-P1.27-LS6.0-BL | TJA1040T/CM,118 | 2 | 立创商城 | https://item.szlcsc.com/7423.html
CN3300 |  | U4 | SOT-23-6_L2.9-W1.6-P0.95-LS2.8-BR | CN3300 | 1 | 立创商城 | https://item.szlcsc.com/53389.html
CM1010-A |  | U5, U6, U7 | SOT-23-6_L2.9-W1.6-P0.95-LS2.8-BR | CM1010-A | 3 | 立创商城 | https://item.szlcsc.com/2785219.html
ESP32-PICO-D4 |  | U8, U9 | QFN-48_L7.0-W7.0-P0.50-BL-EP5.4 | ESP32-PICO-D4 | 2 | 淘宝 | https://item.taobao.com/item.htm?spm=a1z09.2.0.0.40582e8dWqLc0W&id=635409903966&_u=m1jbj7pb7fbc
DRV8313PWPR |  | U10, U11, U12 | HTSSOP-28_L9.8-W4.5-P0.65-LS6.6-BL-EP | DRV8313PWPR | 3 | 立创商城 | https://item.szlcsc.com/93675.html
TPS5430DDAR |  | U13 | SOIC-8_L5.0-W4.0-P1.27-LS6.0-BL-EP2.0 | TPS5430DDAR | 1 | 立创商城 | https://item.szlcsc.com/10396.html
AMS1117-3.3V |  | U14 | SOT-223_L6.5-W3.5-P2.30-LS7.0-BR | AMS1117-3.3V | 1 | 立创商城 | https://item.szlcsc.com/184775.html
TYPE-C16PIN |  | USB1 | TYPE-C16PIN | TYPE-C16PIN | 1 | 立创商城 | https://item.szlcsc.com/2901843.html

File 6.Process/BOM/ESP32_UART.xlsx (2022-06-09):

Comment | Description | Designator | Footprint | LibRef | Quantity | 途径 | 链接
10uF (106) 20% 6.3V | 贴片电容 | C1, C2 | 0402_C | 0402 10uF (106) 20% 6.3V | 2 | 立创商城 | https://item.szlcsc.com/16204.html
100nF (104) 10% 16V | 贴片电容 | C3 | 0402_C | 0402 100nF (104) 10% 16V | 1 | 立创商城 | https://item.szlcsc.com/107097.html
LESD5D5.0CT1G |  | D1, D4, D5 | SOD-523_L1.2-W0.8-LS1.6-BI | LESD5D5.0CT1G | 3 | 立创商城 | https://item.szlcsc.com/356518.html
1N5819W |  | D2 | SOD123 | 1N5819W | 1 | 立创商城 | https://item.szlcsc.com/974466.html
红灯 0603 | 发光二极管 | D3, D7 | 0603_LED_S1 | 0603 红灯 | 2 | 立创商城 | https://item.szlcsc.com/85432.html
蓝灯 0603 | 发光二极管 | D6 | 0603_LED_S1 | 0603 蓝灯 | 1 | 立创商城 | https://item.szlcsc.com/85435.html
ESD5Z3.3C |  | D8, D9, D10, D11, D12 | SOD-523_L1.2-W0.8-LS1.6-BI | ESD5Z3.3C | 5 | 立创商城 | https://item.szlcsc.com/515057.html
BSMD0805-110-6V |  | F1 | F0805 | JK | 1 | 立创商城 | https://item.szlcsc.com/947788.html
HDR1.27-LI-6P |  | P1 | HDR1.27-LI-6P | HDR1.27-LI-6P | 1 | 立创商城 | https://item.szlcsc.com/3809.html
SS8050 |  | Q1, Q2 | SOT-23-3_L2.9-W1.3-P1.90-LS2.4-BR | SS8050 | 2 | 立创商城 | https://item.szlcsc.com/192557.html
5.1KΩ (5101) ±1% | 贴片电阻 | R1, R3 | 0402_R | 0402 5.1KΩ (5101) 1% | 2 | 立创商城 | https://item.szlcsc.com/3180387.html
1KΩ (1001) ±1% | 贴片电阻 | R2, R6, R7 | 0402_R | 0402 1KΩ (1001) 1% | 3 | 立创商城 | https://item.szlcsc.com/3180377.html
100Ω (1000) ±1% | 贴片电阻 | R4, R5 | 0402_R | 0402 100Ω (1000) 1% | 2 | 立创商城 | https://item.szlcsc.com/103962.html
10KΩ (1002) ±1% | 贴片电阻 | R8, R9 | 0402_R | 0402 10KΩ (1002) 1% | 2 | 立创商城 | https://item.szlcsc.com/3180374.html
TP |  | TP1, TP2, TP3, TP4 | TP_1X1MM | TP | 4 | 立创商城 | 不需要
AMS1117-3.3V |  | U1 | SOT-223_L6.5-W3.5-P2.30-LS7.0-BR | AMS1117-3.3V | 1 | 立创商城 | https://item.szlcsc.com/184775.html
CH340C |  | U2 | SOP-16_L10.0-W3.9-P1.27-LS6.0-BL | CH340C | 1 | 立创商城 | https://item.szlcsc.com/85852.html
TYPE-C16PIN |  | USB1 | TYPE-C16PIN | TYPE-C16PIN | 1 | 立创商城 | https://item.szlcsc.com/2901843.html

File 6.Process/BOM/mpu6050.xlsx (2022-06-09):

Comment | Description | Designator | Footprint | LibRef | Quantity | 途径 | 链接
2.2uF ±10％ 16V | 贴片电容 | C3 | 0402_C | 0402 100nF (104) 10% 16V | 1 | 立创商城 | https://item.szlcsc.com/306650.html
10nF (103) 10% 50V | 贴片电容 | C4 | 0402_C | 0402 10nF (103) 10% 50V | 1 | 立创商城 | https://item.szlcsc.com/61185.html
100nF (104) 10% 16V | 贴片电容 | C5, C6 | 0402_C | 0402 100nF (104) 10% 16V | 2 | 立创商城 | https://item.szlcsc.com/107097.html
HC-1.0-5PLT |  | CN1 | CONN-SMD_5P-P1.00_HCTL_HC-1.0-5PLT | HC-1.0-5PLT | 1 | 立创商城 | https://item.szlcsc.com/3039054.html
ESD5Z3.3C |  | D1 | SOD-523_L1.2-W0.8-LS1.6-BI | ESD5Z3.3C | 1 | 立创商城 | https://item.szlcsc.com/515057.html
0Ω (0R0) ±1% | 贴片电阻 | R11 | 0402_R | 0402 0Ω (0R0) 1% | 1 | 立创商城 | https://item.szlcsc.com/305682.html
4.7KΩ (4701) ±1% | 贴片电阻 | R12, R13 | 0402_R | 0402 4.7KΩ (4701) 1% | 2 | 立创商城 | https://item.szlcsc.com/288683.html
1KΩ (1001) ±1% | 贴片电阻 | R14 | 0402_R | 0402 1KΩ (1001) 1% | 1 | 立创商城 | https://item.szlcsc.com/226431.html
MPU-6050_C24112 |  | U3 | QFN-24_L4.0-W4.0-P0.50-BL-EP2.6 | MPU-6050_C24112 | 1 | 淘宝 | https://item.taobao.com/item.htm?spm=a1z10.3-c.w4002-23802692547.9.1b7931e6lObMGo&id=635813221292

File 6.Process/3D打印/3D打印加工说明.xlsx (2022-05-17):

料号 | 数量 | 文件说明
YC.JGJ.000007 | 4 | 角1
YC.JGJ.000008 | 4 | 角2
YC.JGJ.000009.1 | 1 | imu安装板

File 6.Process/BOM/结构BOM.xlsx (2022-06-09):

编号 | 零件名称 | 说明 | 数量 | 总价格 | 链接
1 | 外框 | 2mm玻纤，机加工，黑色 | 6 | 178 | https://item.taobao.com/item.htm?spm=a1z09.2.0.0.418e2e8dkIytgP&id=598622463797&_u=e1jbj7pb4f6e
2 | 电机固定支架_2715电机 | 2mm玻纤，机加工，黑色 | 3
3 | 电池与外框固定架 | 2mm玻纤，机加工，黑色 | 1
4 | 电机连接板_2715电机 | 2mm玻纤，机加工，黑色 | 3
5 | 主控挡线板 | 2mm玻纤，机加工，黑色 | 1
6 | 飞轮_2715电机 | 4mm304不锈钢，激光切割，磨砂红烤漆 | 3 | 75 | https://shop118439180.taobao.com/?spm=a230r.7195193.1997079397.2.69c75e91nPd2E0
7 | 角1 | 未来工厂3D打印，未来8100材料，米白色，需要自行攻丝 | 4 | 45 | https://www.wenext.cn/
8 | 角2 | 未来工厂3D打印，未来8100材料，米白色，需要自行攻丝 | 4
9 | IMU安装板 | 未来工厂3D打印，未来8100材料，米白色，需要自行攻丝 | 1
10 | 402764电池 | 1000mA，3.7V，PH2.0反向插，白色 | 3 | 44.4 | https://item.taobao.com/item.htm?spm=a1z09.2.0.0.7f892e8dh74HJA&id=39406146740&_u=d1jbj7pbaf70
11 | 2715电机（不带径向磁铁） | 银白色 | 3 | 50.64 | https://item.taobao.com/item.htm?spm=a1z09.2.0.0.7f892e8dh74HJA&id=597275437810&_u=d1jbj7pb3366
12 | 径向磁铁D7*d3*d3 | 白色 | 3 | 10.8 | https://item.taobao.com/item.htm?spm=a1z09.2.0.0.413a2e8dKo5tt3&id=580731710287&_u=d1jbj7pb727a
13 | M2.5 D4 12mm通孔铝柱 | 阳极氧化黑色，预算不足可用铜柱替换 | 14 | 79 | https://detail.tmall.com/item.htm?id=609497872989&_u=d1jbj7pbbc07&skuId=4455491374265
14 | M2.5 D4 8mm通孔铝柱 |  | 20 |  | https://detail.tmall.com/item.htm?id=609497872989&_u=d1jbj7pbbc07&skuId=4455491374263
15 | M2 D3.5 6mm通孔铝柱 |  | 12 |  | https://detail.tmall.com/item.htm?id=610201851065&_u=d1jbj7pb9c9d&skuId=4287786833554
16 | M2.5 D4 6mm通孔铝柱 |  | 2 |  | https://detail.tmall.com/item.htm?id=609497872989&_u=d1jbj7pbbc07&skuId=4455491374262
17 | 圆头内六角螺丝_M2.5 X 4mm_L不包含头部_P0.45 | 高碳钢，黑色 | 11 | 3.6 | https://detail.tmall.com/item.htm?id=16979965616&_u=d1jbj7pb6d6d&skuId=4915411014656
18 | 圆头内六角螺丝_M2.5 X 5mm_L不包含头部_P0.45 |  | 38 | 3.6 | https://detail.tmall.com/item.htm?id=16979965616&_u=d1jbj7pb6d6d&skuId=4915411014651
19 | 沉头十字螺丝_M2.5 X L6mm_L包含头部_P0.45 |  | 45 | 2.44 | https://detail.tmall.com/item.htm?id=15817314764&_u=d1jbj7pbb89d&skuId=33508310712
20 | 机米顶丝M2.5x5mm | 白色 | 2 | 2.94 | https://detail.tmall.com/item.htm?id=16948094393&_u=d1jbj7pb3aba&skuId=4683423875195
21 | 内六角杯头螺丝_M1.5x12mm_不包含头部 | 白色 | 12 | 11 | https://item.taobao.com/item.htm?spm=a1z09.2.0.0.7f892e8dh74HJA&id=543017651845&_u=d1jbj7pb90b1
22 | 内六角杯头螺丝_M1.5x6mm_不包含头部 |  | 12 | 8
23 | SHR1.0MM双头连接线 7P | 反向接法，100mm | 3 | 3.48 | https://item.taobao.com/item.htm?spm=a1z09.2.0.0.7f892e8dh74HJA&id=581255230378&_u=d1jbj7pb9ace
24 | SHR1.0MM双头连接线 5P | 同向接法，50mm | 1 | 0.7
25 | 猫头魔术轧带（绑点电池） | 长14.5CM，宽1.1CM | 2 | 9 | https://item.taobao.com/item.htm?spm=a1z09.2.0.0.7f892e8dh74HJA&id=648075806334&_u=d1jbj7pb9847
26 | 热缩管（把3个电池固定一起） | 黑色直径25mm/1m | 1 | 5 | https://item.taobao.com/item.htm?spm=a1z09.2.0.0.7f892e8dh74HJA&id=540003839582&_u=d1jbj7pb9740
27 | 黑色尼龙扎带 3*100MM（扎线）（不扎线可不买） | 黑色 | 2 | 5.9 | https://item.taobao.com/item.htm?id=527899451690&ns=1&abbucket=8 (https://item.taobao.com/item.htm?spm=a230r.1.14.23.48c372e9QR98Wf&id=527899451690&ns=1&abbucket=8)
 | 502胶水 | 粘径向磁铁，小卖部买，不行就淘宝 | 1 | 2.9 | https://detail.tmall.com/item.htm?id=628345475388&ali_trackid=1_4b2890d266925e68e6717938439ef40f
28 | （可选）丝杆扳手，攻牙 | 已有可不购买 | 1 | 10.29 | https://detail.tmall.com/item.htm?id=21799076398&_u=d1jbj7pbcb9c&skuId=4939030495815
29 | （可选）手用丝锥，M2.5*0.45 | 已有可不购买，可以选择更便宜的购买，能用就行 | 1 | 35 | https://detail.tmall.com/item.htm?id=15818480349&_u=d1jbj7pb4001&skuId=18175442261
 |  |  |  | 541.4 | 不含攻牙套装

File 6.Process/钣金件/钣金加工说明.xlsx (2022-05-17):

名称 | 材料 | 数量 | 作用 | 备注
YC.JGJ.000001 | 2mm玻纤板 | 6 | 外框 | 需要做M2.5沉孔
YC.JGJ.000003 | 2mm玻纤板 | 3 | 电机固定支架_2715电机
YC.JGJ.000004 | 2mm玻纤板 | 3 | 电机连接板_2715电机
YC.JGJ.000005 | 2mm玻纤板 | 1 | 主控挡线板
YC.JGJ.000006 | 2mm玻纤板 | 1 | 电池与外框固定架子
YC.JGJ.000002 | 4mm304不锈钢 | 3 | 飞轮_2715电机 | 磨砂烤漆红

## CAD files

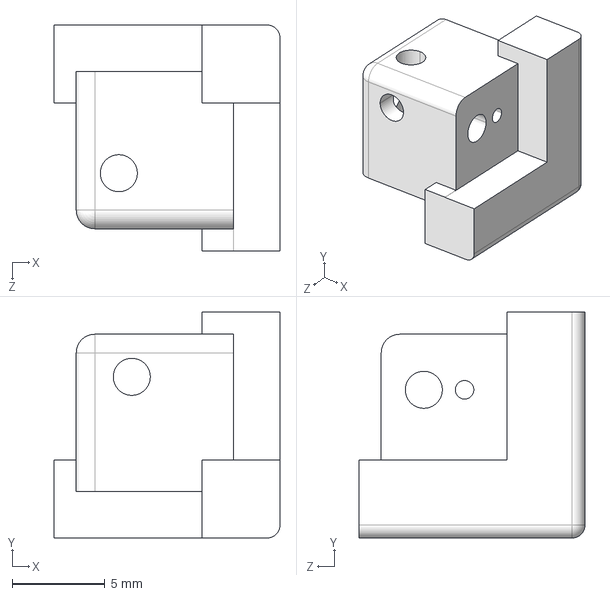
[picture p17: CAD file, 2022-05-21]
6.Process/3D打印/YC.JGJ.000008.STEP
12.2 x 12.2 x 12.2 mm

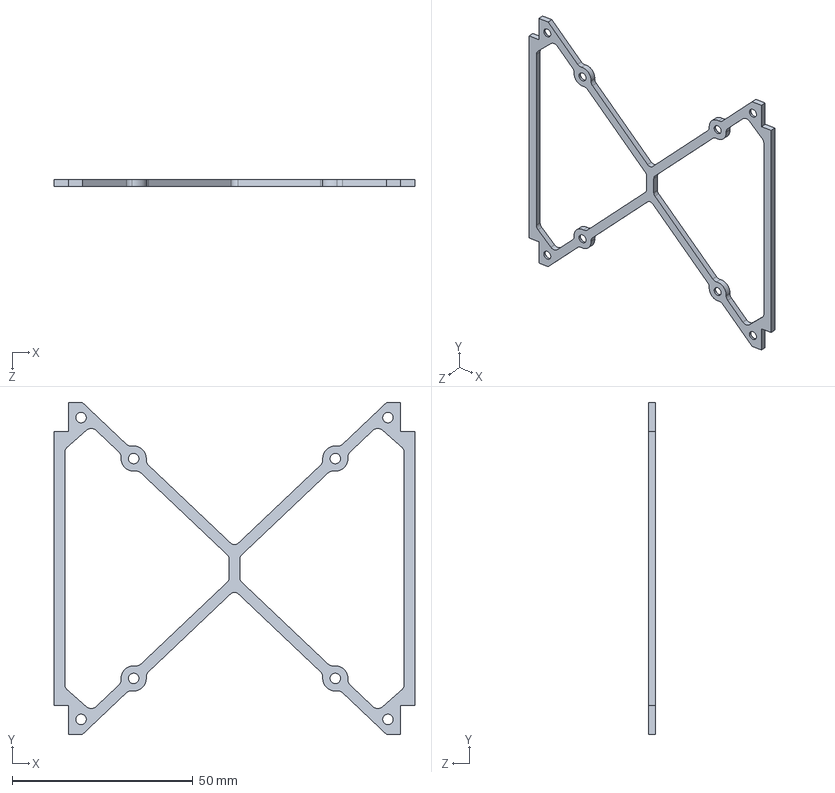
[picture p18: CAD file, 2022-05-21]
6.Process/钣金件/YC.JGJ.000001.STEP
100.0 x 92.0 x 2.00 mm

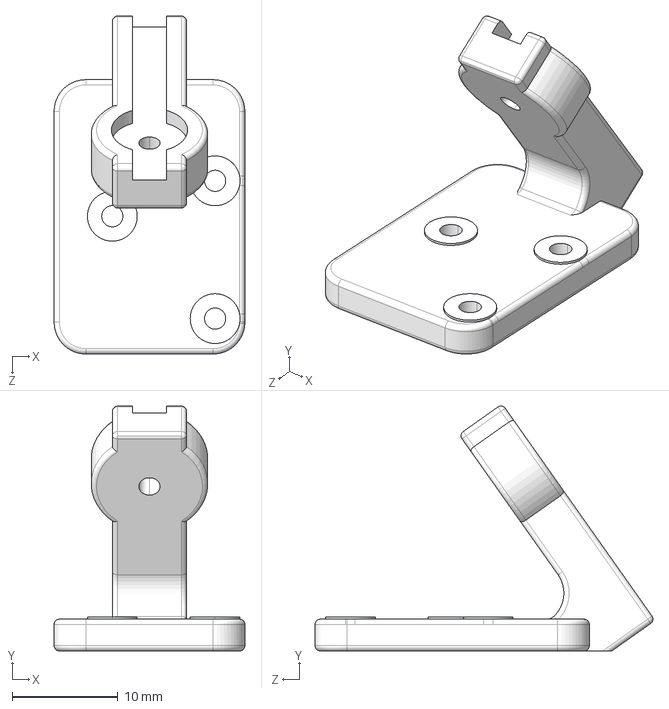
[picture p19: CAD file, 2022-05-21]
6.Process/3D打印/YC.JGJ.000009.1.STEP
18.0 x 23.1 x 31.9 mm

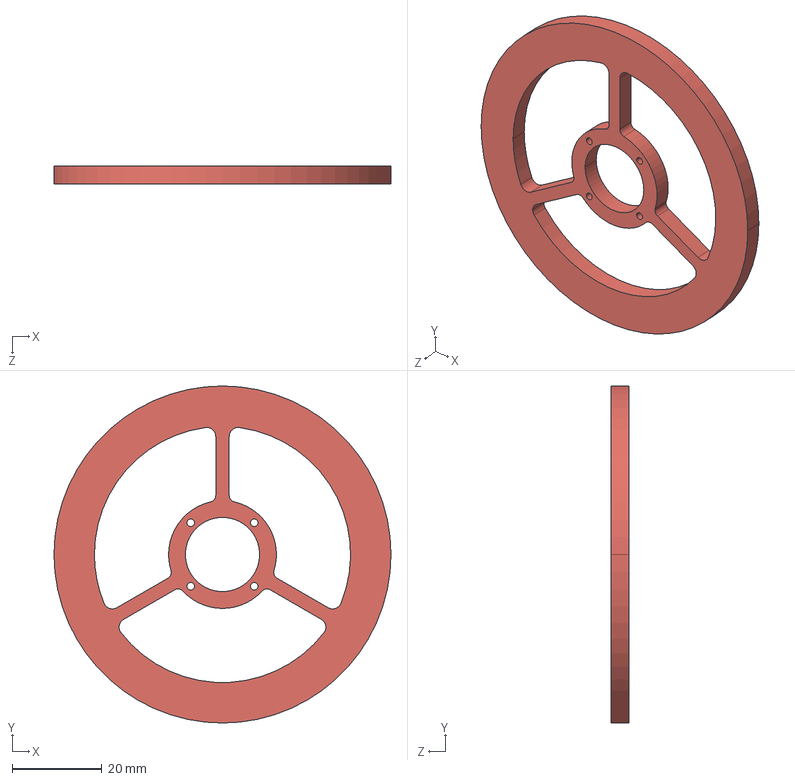
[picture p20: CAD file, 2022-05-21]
6.Process/钣金件/YC.JGJ.000002.4.STEP
75.0 x 75.0 x 4.00 mm

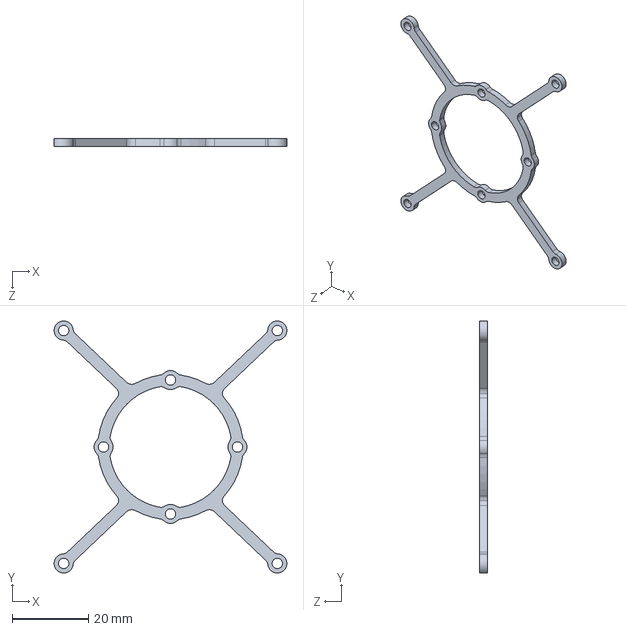
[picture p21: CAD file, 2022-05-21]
6.Process/钣金件/YC.JGJ.000003.STEP
60.9 x 65.9 x 2.00 mm

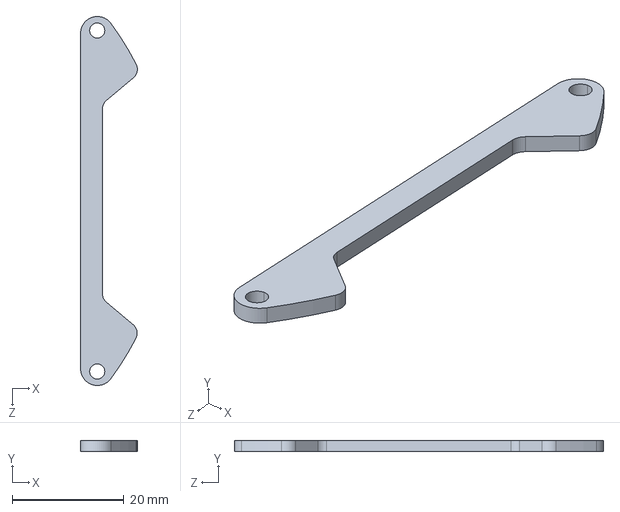
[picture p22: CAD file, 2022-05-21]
6.Process/钣金件/YC.JGJ.000005.STEP
10.1 x 2.00 x 65.9 mm

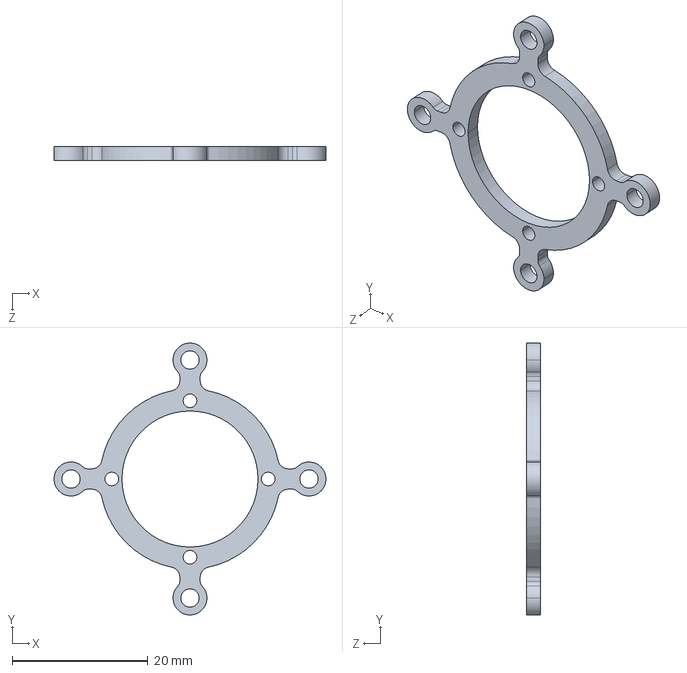
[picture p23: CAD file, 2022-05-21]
6.Process/钣金件/YC.JGJ.000004.STEP
40.0 x 40.0 x 2.00 mm

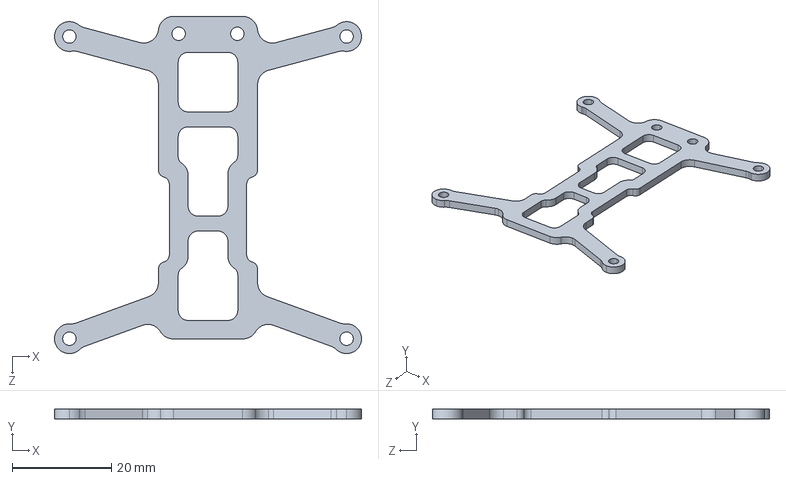
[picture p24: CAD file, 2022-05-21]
6.Process/钣金件/YC.JGJ.000006.STEP
61.9 x 2.00 x 67.9 mm

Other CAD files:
6.Process/3D打印/YC.JGJ.000007.STEP
6.Process/3D打印/YC.JGJ.000007.STL
6.Process/3D打印/YC.JGJ.000008.STL
6.Process/3D打印/YC.JGJ.000009.1.STL
6.Process/钣金件/YC.JGJ.000001.DWG
6.Process/钣金件/YC.JGJ.000002.4.DWG
6.Process/钣金件/YC.JGJ.000003.DWG
6.Process/钣金件/YC.JGJ.000004.DWG
6.Process/钣金件/YC.JGJ.000005.DWG
6.Process/钣金件/YC.JGJ.000006.DWG

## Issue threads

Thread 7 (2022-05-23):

BOM表问题

qxzg, 2022-05-23:
1. `结构bom.xls`中第24行的`SHR1.0MM双头连接线 10P`线应该改为`7p`吧，我看pcb文件里控制板和AS5600之间的连接用的是7pin的连接座，没有看到10pin的。
2. 另外14-17行中的`M2.5 D4通孔铝柱_2x12mm`里的`_2`是不是是多余的啊。

ZhaJiHu, 2022-05-23:
SHR1.0MM双头连接线 没有10P的，只有7P的

ZhaJiHu, 2022-05-23:
麻烦新建一个分支，命名为：#7，推送上来再提交merge request

ZhaJiHu, 2022-05-24:
已经merge

Closed 2022-05-24.

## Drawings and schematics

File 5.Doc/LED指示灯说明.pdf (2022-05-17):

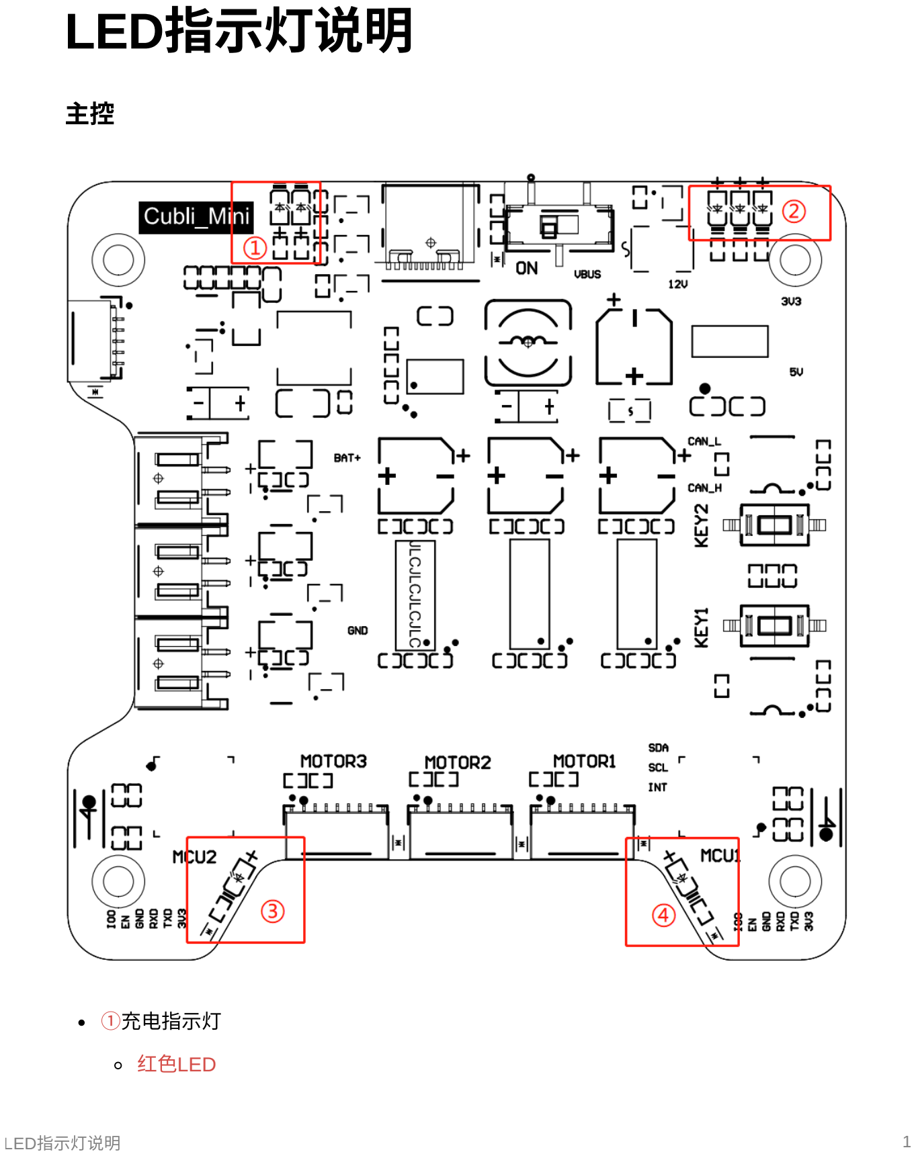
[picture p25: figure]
LED指⽰灯说明; ①充电指⽰灯; 红⾊LED

### 绿⾊LED

### 红⾊LED

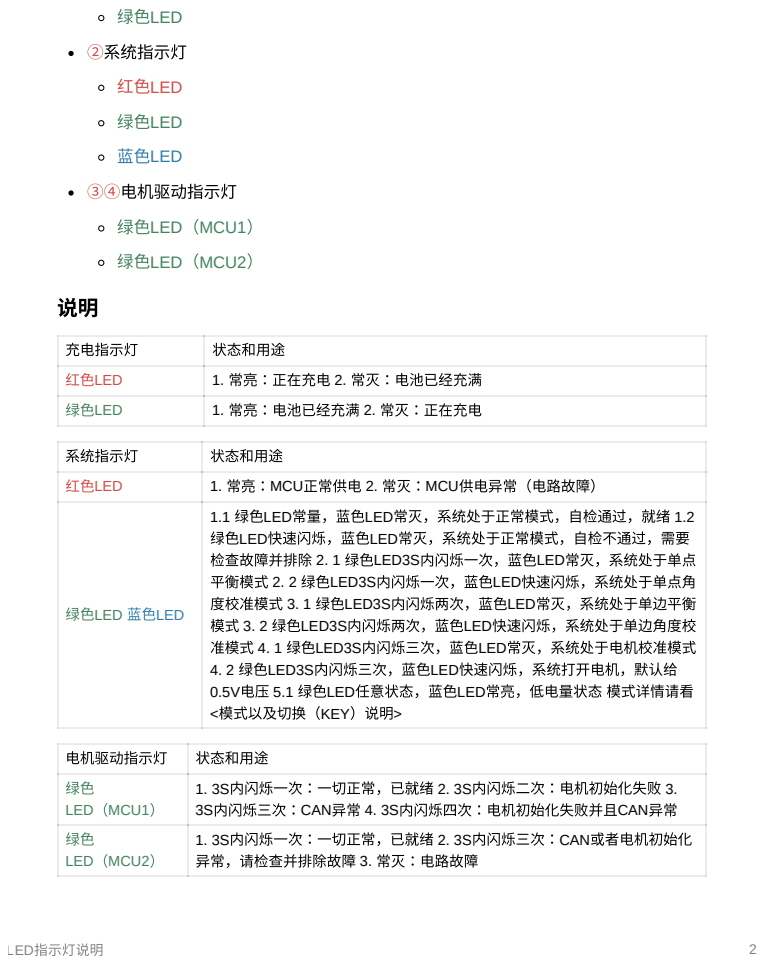
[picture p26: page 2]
LED指⽰灯说明; ②系统指⽰灯; 绿⾊LED; 蓝⾊LED; ③④电机驱动指⽰灯; 绿⾊LED（MCU1）; 绿⾊LED（MCU2）

充电指⽰灯 | 状态和⽤途

红⾊LED | 1. 常亮：正在充电 2. 常灭：电池已经充满

绿⾊LED | 1. 常亮：电池已经充满 2. 常灭：正在充电

系统指⽰灯 | 状态和⽤途

红⾊LED | 1. 常亮：MCU正常供电 2. 常灭：MCU供电异常（电路故障）
绿⾊LED 蓝⾊LED | 1.1 绿⾊LED常量，蓝⾊LED常灭，系统处于正常模式，⾃检通过，就绪 1.2 绿⾊LED快速闪烁，蓝⾊LED常灭，系统处于正常模式，⾃检不通过，需要 检查故障并排除 2. 1 绿⾊LED3S内闪烁⼀次，蓝⾊LED常灭，系统处于单点 平衡模式 2. 2 绿⾊LED3S内闪烁⼀次，蓝⾊LED快速闪烁，系统处于单点⾓ 度校准模式 3. 1 绿⾊LED3S内闪烁两次，蓝⾊LED常灭，系统处于单边平衡 模式 3. 2 绿⾊LED3S内闪烁两次，蓝⾊LED快速闪烁，系统处于单边⾓度校 准模式 4. 1 绿⾊LED3S内闪烁三次，蓝⾊LED常灭，系统处于电机校准模式 4. 2 绿⾊LED3S内闪烁三次，蓝⾊LED快速闪烁，系统打开电机，默认给 0.5V电压 5.1 绿⾊LED任意状态，蓝⾊LED常亮，低电量状态 模式详情请看 <模式以及切换（KEY）说明>

电机驱动指⽰灯 | 状态和⽤途

绿⾊ LED（MCU1） | 1. 3S内闪烁⼀次：⼀切正常，已就绪 2. 3S内闪烁⼆次：电机初始化失败 3. 3S内闪烁三次：CAN异常 4. 3S内闪烁四次：电机初始化失败并且CAN异常

绿⾊ LED（MCU2） | 1. 3S内闪烁⼀次：⼀切正常，已就绪 2. 3S内闪烁三次：CAN或者电机初始化 异常，请检查并排除故障 3. 常灭：电路故障

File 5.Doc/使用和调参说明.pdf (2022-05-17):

# 使⽤和调参说明

## 开机流程

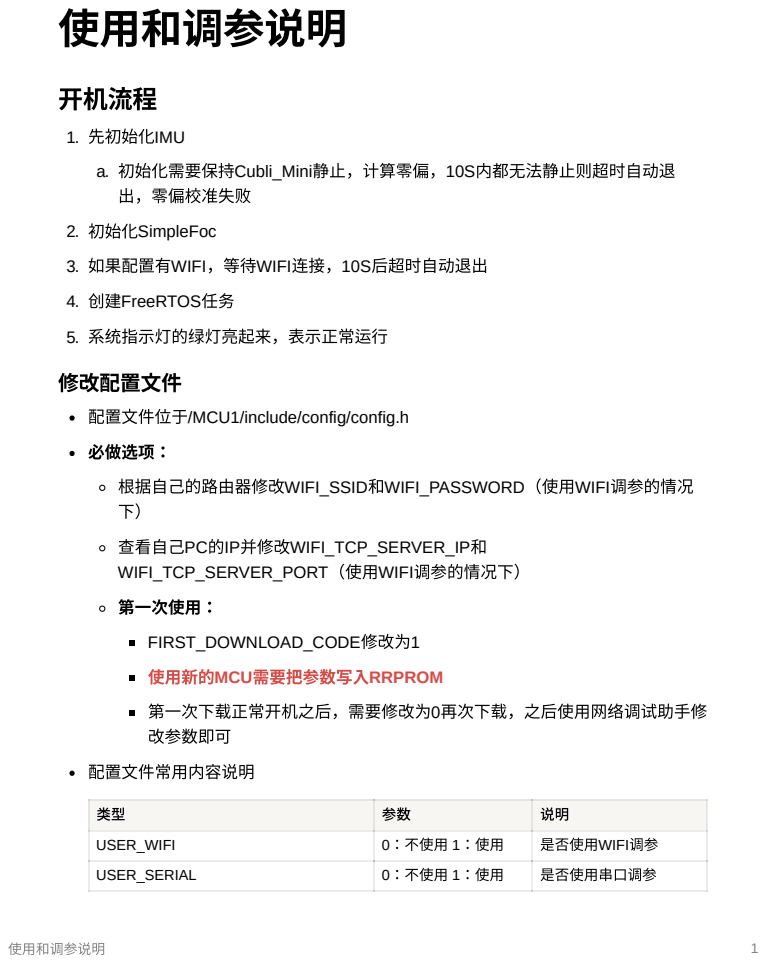
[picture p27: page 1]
使⽤和调参说明; 1. 先初始化IMU; 必做选项：; 根据⾃⼰的路由器修改WIFI_SSID和WIFI_PASSWORD（使⽤WIFI调参的情况; 查看⾃⼰PC的IP并修改WIFI_TCP_SERVER_IP和 WIFI_TCP_SERVER_PORT（使⽤WIFI调参的情况下）; FIRST_DOWNLOAD_CODE修改为1; 使⽤新的MCU需要把参数写⼊RRPROM

a. 初始化需要保持Cubli_Mini静⽌，计算零偏，10S内都⽆法静⽌则超时⾃动退
出，零偏校准失败
2. 初始化SimpleFoc

3. 如果配置有WIFI，等待WIFI连接，10S后超时⾃动退出
4. 创建FreeRTOS任务

5. 系统指⽰灯的绿灯亮起来，表⽰正常运⾏

修改配置⽂件
配置⽂件位于/MCU1/include/config/config.h

第⼀次下载正常开机之后，需要修改为0再次下载，之后使⽤⽹络调试助⼿修
改参数即可

配置⽂件常⽤内容说明

类型 | 参数 | 说明
USER_WIFI | 0：不使⽤ 1：使⽤ | 是否使⽤WIFI调参

USER_SERIAL | 0：不使⽤ 1：使⽤ | 是否使⽤串⼝调参

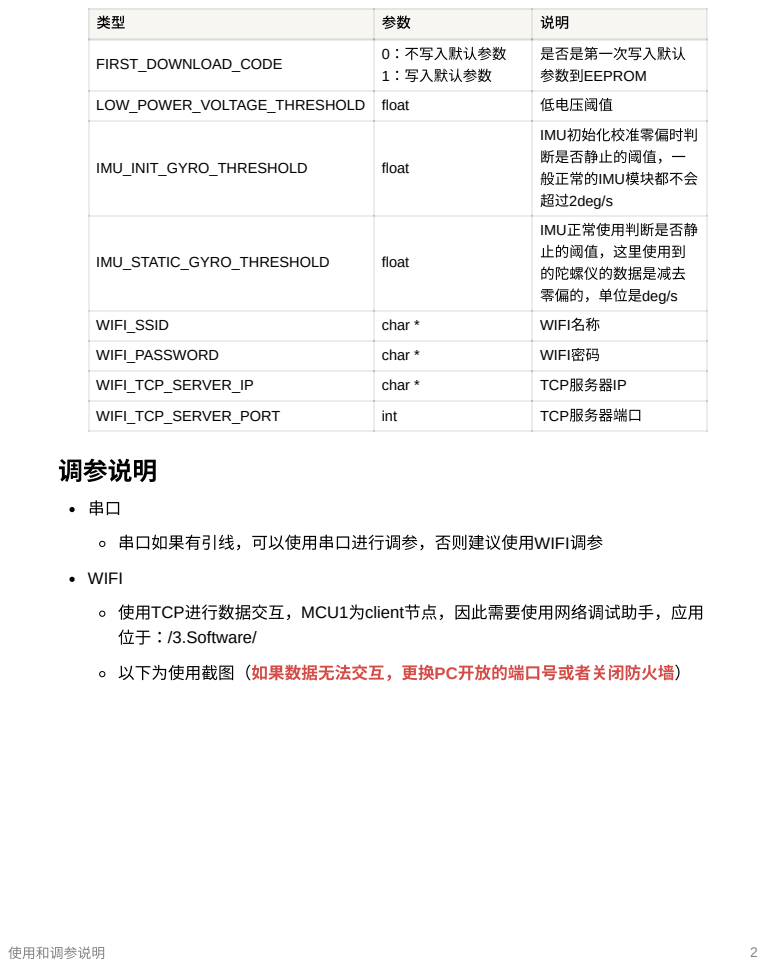
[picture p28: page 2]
调参说明

FIRST_DOWNLOAD_CODE | 0：不写⼊默认参数 1：写⼊默认参数 | 是否是第⼀次写⼊默认 参数到EEPROM

LOW_POWER_VOLTAGE_THRESHOLD | float | 低电压阈值
IMU_INIT_GYRO_THRESHOLD | float | IMU初始化校准零偏时判 断是否静⽌的阈值，⼀ 般正常的IMU模块都不会 超过2deg/s

IMU_STATIC_GYRO_THRESHOLD | float | IMU正常使⽤判断是否静 ⽌的阈值，这⾥使⽤到 的陀螺仪的数据是减去 零偏的，单位是deg/s

WIFI_SSID | char * | WIFI名称
WIFI_PASSWORD | char * | WIFI密码
WIFI_TCP_SERVER_IP | char * | TCP服务器IP
WIFI_TCP_SERVER_PORT | int | TCP服务器端⼝

串⼝如果有引线，可以使⽤串⼝进⾏调参，否则建议使⽤WIFI调参
WIFI

使⽤TCP进⾏数据交互，MCU1为client节点，因此需要使⽤⽹络调试助⼿，应⽤
位于：/3.Software/

以下为使⽤截图（如果数据⽆法交互，更换PC开放的端⼝号或者关闭防⽕墙）

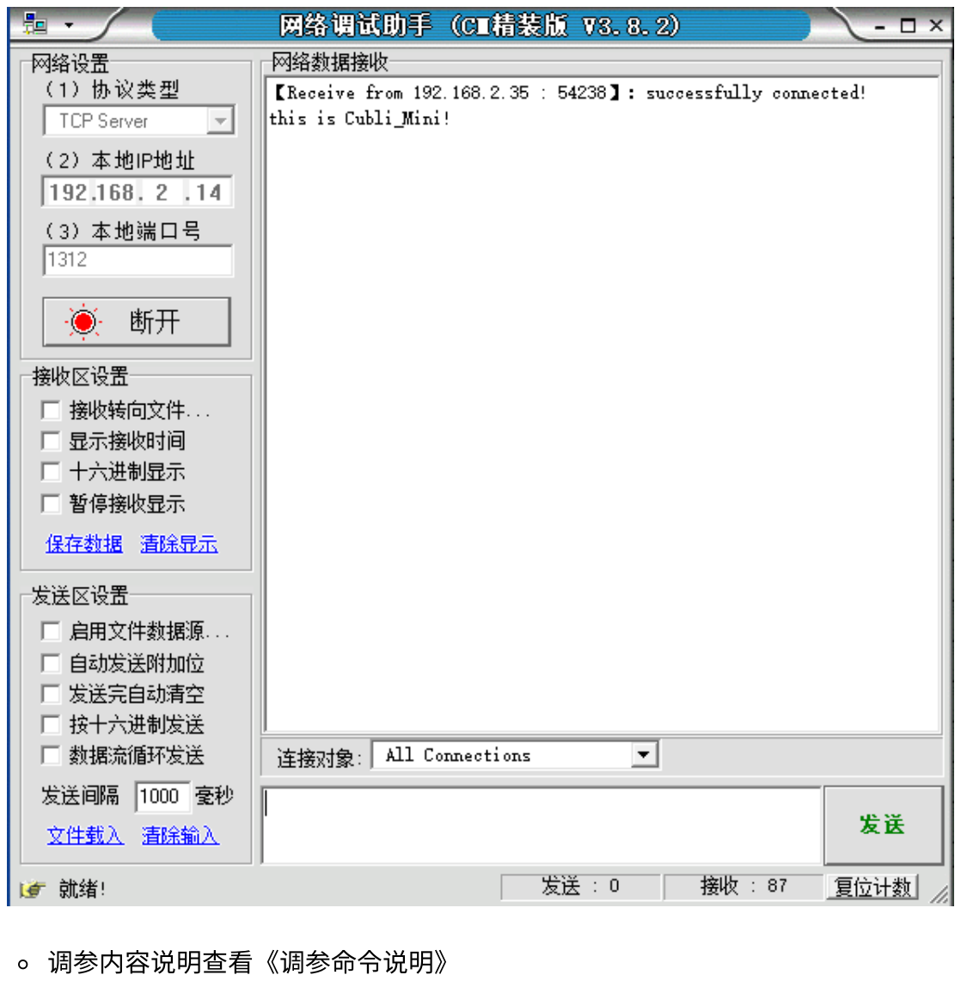
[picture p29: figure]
调参内容说明查看《调参命令说明》

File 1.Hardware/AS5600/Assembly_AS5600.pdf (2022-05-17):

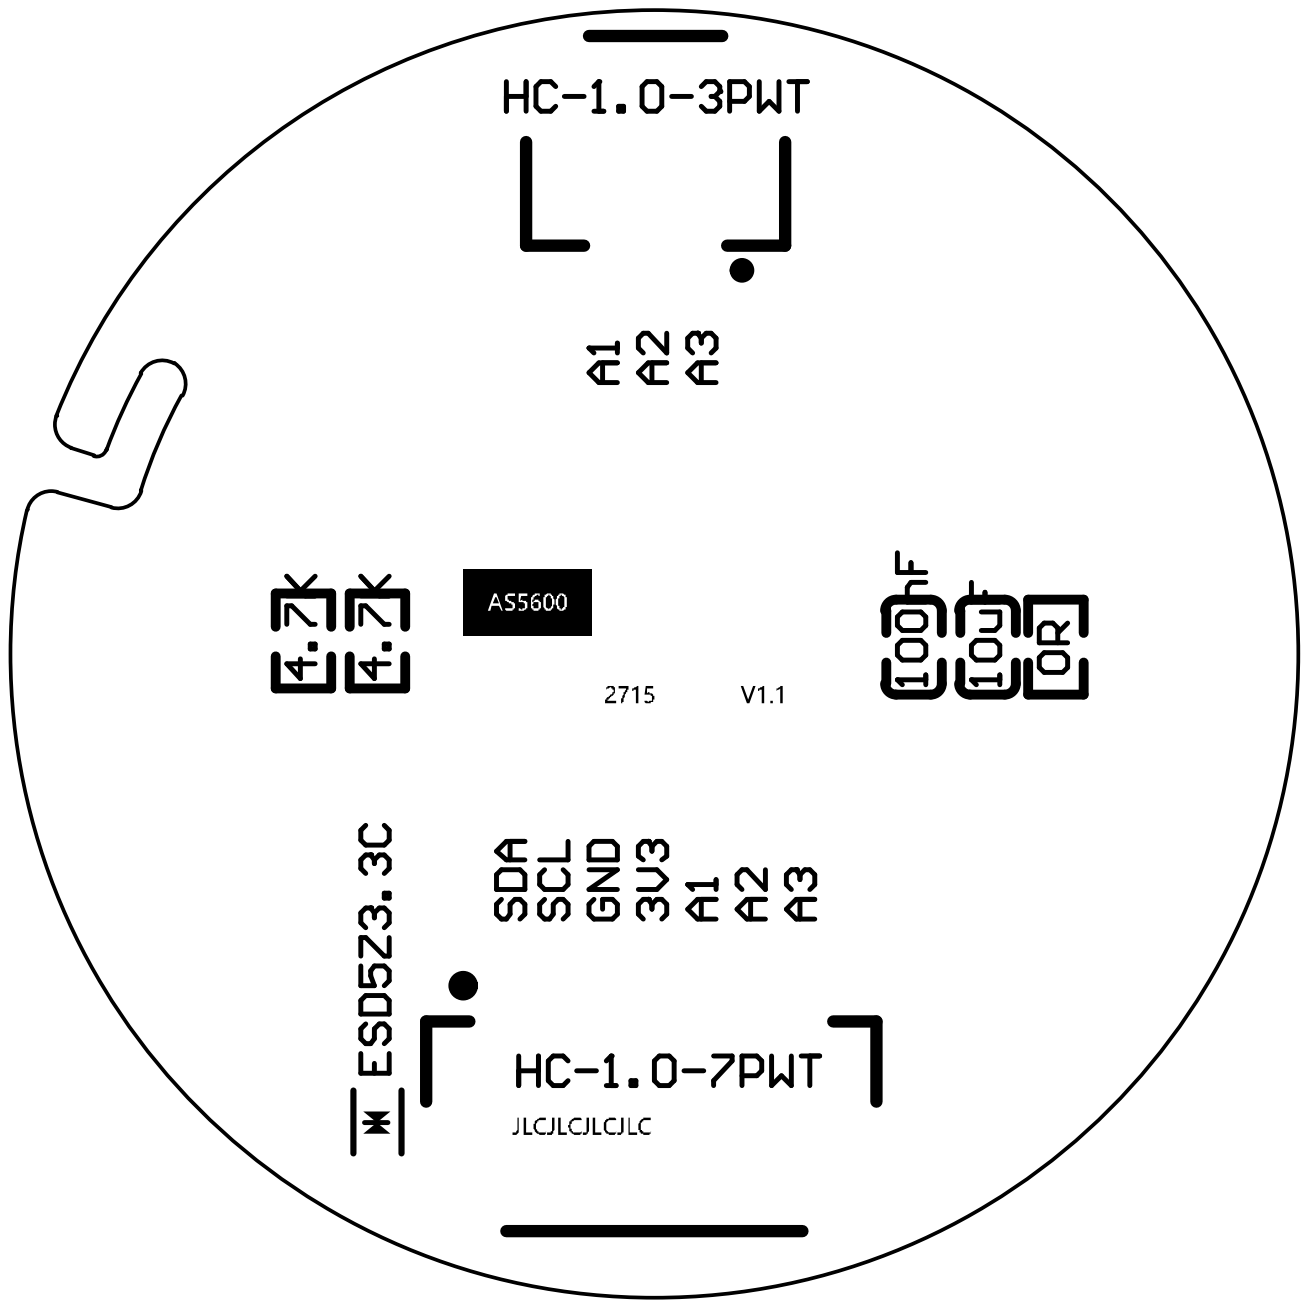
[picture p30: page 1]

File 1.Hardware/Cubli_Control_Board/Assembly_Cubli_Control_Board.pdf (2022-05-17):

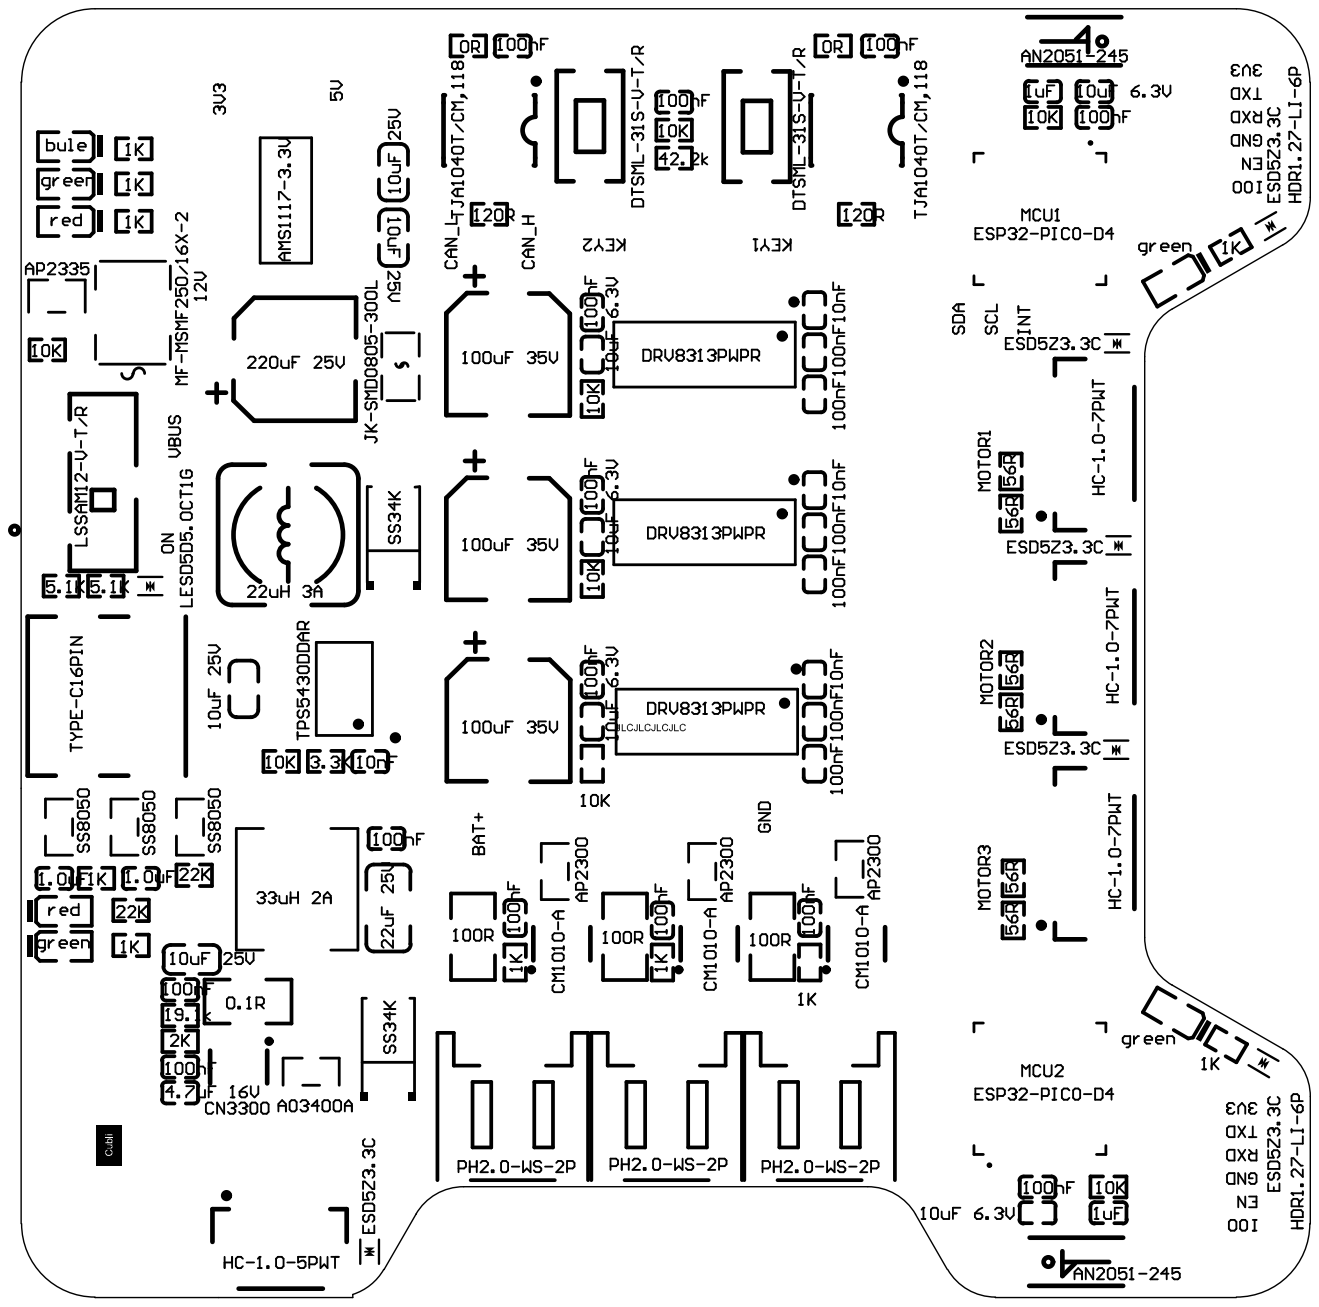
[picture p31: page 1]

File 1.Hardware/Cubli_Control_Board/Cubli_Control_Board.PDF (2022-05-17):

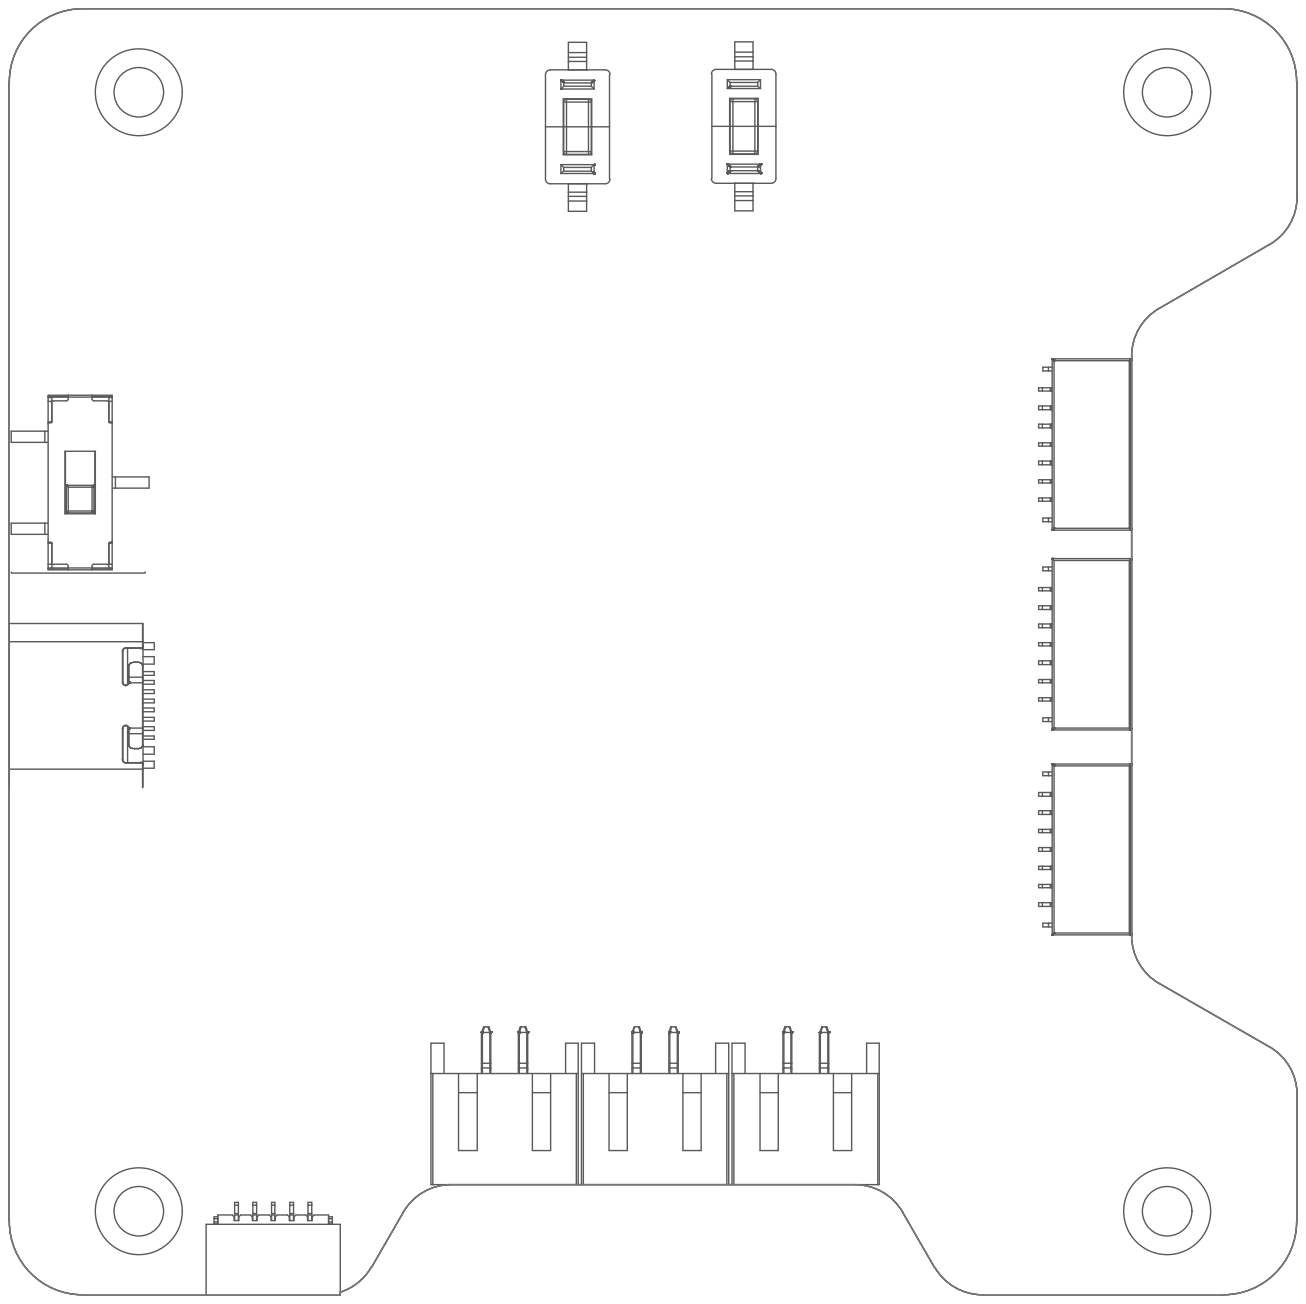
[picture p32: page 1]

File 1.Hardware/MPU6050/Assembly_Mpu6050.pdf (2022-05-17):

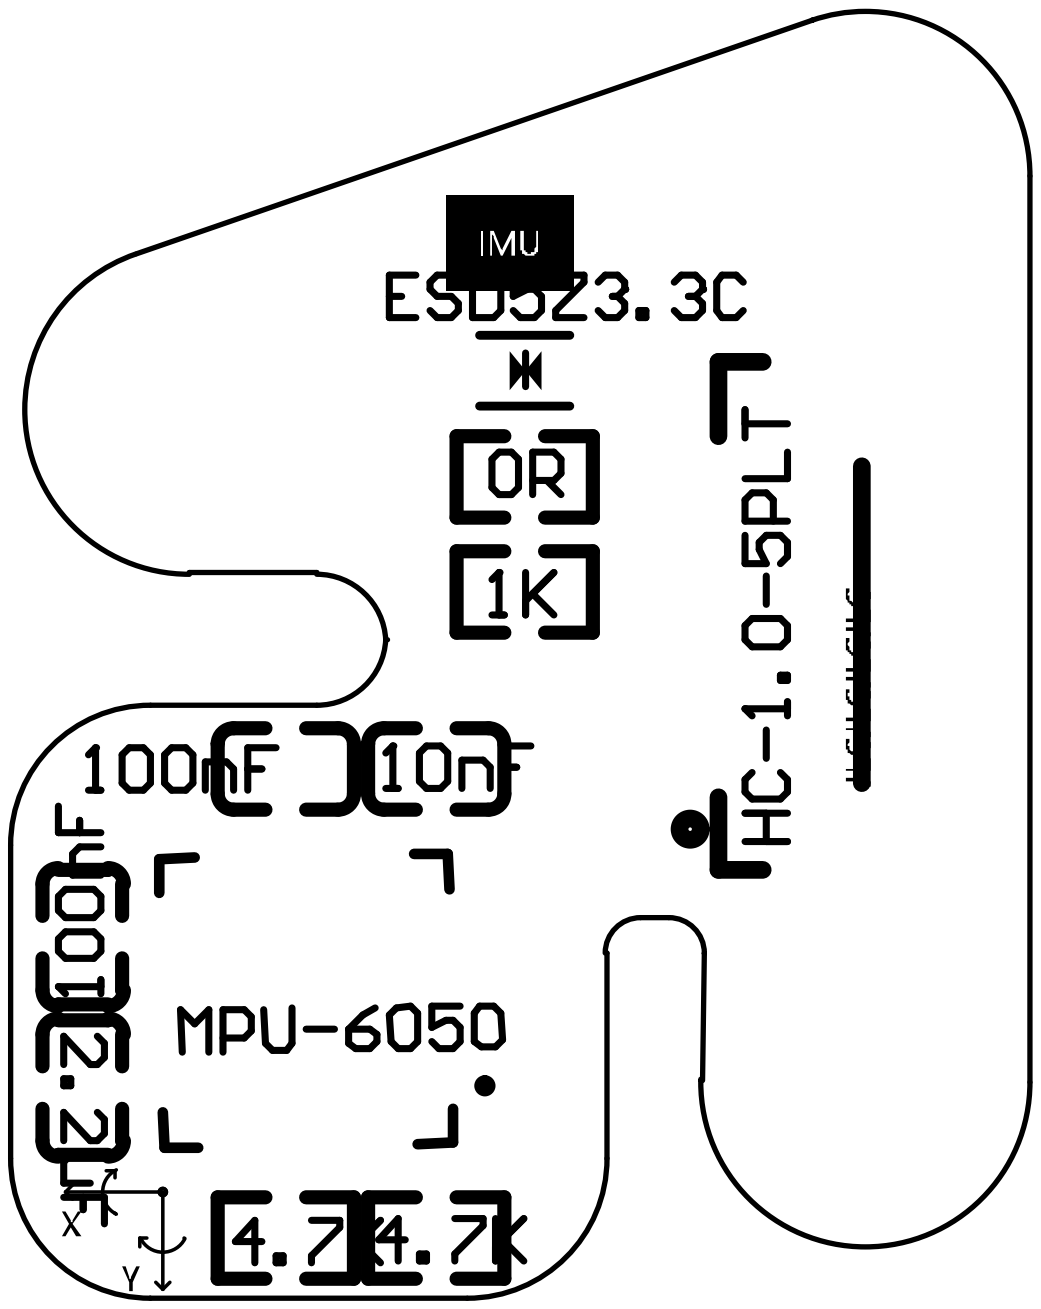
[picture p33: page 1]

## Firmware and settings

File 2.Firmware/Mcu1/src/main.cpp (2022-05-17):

#include <Arduino.h>
#include <SimpleFOC.h>
#include "imu/ahrs.h"
#include "bsp/bsp_driver.h"
#include "bsp/can.h"
#include "control/serial_commander.h"
#include "control/cubli_mini.h"
#include "control/wifi_commander.h"
#include "control/param.h"

using namespace CubliMini::Imu;
using namespace CubliMini::ImuDriver;
using namespace CubliMini::Control;

AHRS ahrs;
SerialCommander serial_commander;
CubliMiniControl cubli_mini;
WifiCommander wifi_commander;

MagneticSensorI2C sensor1 = MagneticSensorI2C(AS5600_I2C);
// BLDC motor & driver instance
BLDCMotor motor1 = BLDCMotor(MOTOR_PP);
// motor1
BLDCDriver3PWM driver1 = BLDCDriver3PWM(MOTOR_1_PWM1_PIN, MOTOR_1_PWM2_PIN, MOTOR_1_PWM3_PIN, MOTOR_1_EN_PIN);
// i2c
TwoWire motor1_i2c = TwoWire(0);
TwoWire imu_i2c = TwoWire(1);

SemaphoreHandle_t x_mutex;

float ch1_target_velocity = 0;
// instantiate the commander
Commander command = Commander(Serial);
void doMotor(char* cmd) { command.motor(&motor1, cmd); }
void ch1doTarget(char* cmd) { command.scalar(&ch1_target_velocity, cmd); }

void CanTask(void *parameter);
void WifiCommanderTask(void *parameter);
void ControlTask(void *parameter);
void ModecontrolTask(void *parameter);
void SerialCmdTask(void *parameter);
void SensorUpdateTask(void *parameter);
void SerialLogTask(void *parameter);
void SimpleFocInit();


void setup()
{
  Serial.begin(115200);
  ahrs.mpu6050_driver.Init(&imu_i2c);
  cubli_mini.LinkSensor(&ahrs);
  cubli_mini.Init();
  SimpleFocInit();
  x_mutex = xSemaphoreCreateMutex();
#if USER_WIFI
  wifi_commander.ConnectWifi();
  if(wifi_commander.GetConnectStatus() == WifiConnectStatus_e::eWIFI_SUCCESS)
  {
      wifi_commander.LinkMutex(&x_mutex);
  }
#endif
#if FIRST_DOWNLOAD_CODE
  // 第一次烧录芯片的时候需要
  cubli_mini.FirstWriteParamToEeprom();
#endif 
  // core 0
#if USER_WIFI
  if(wifi_commander.GetConnectStatus() == WifiConnectStatus_e::eWIFI_SUCCESS)
  {
      xTaskCreatePinnedToCore(WifiCommanderTask, "WifiCommanderTask", 20000, NULL, 6, NULL, 0);
  }
#endif

  // core 1
  xTaskCreatePinnedToCore(ModecontrolTask, "ModecontrolTask", 10000, NULL, 6, NULL, 1);
  xTaskCreatePinnedToCore(SerialLogTask, "SerialLogTask", 10000, NULL, 5, NULL, 1);
  xTaskCreatePinnedToCore(SerialCmdTask, "SerialCmdTask", 10000, NULL, 4, NULL, 1);
  xTaskCreatePinnedToCore(ControlTask, "ControlTask", 20000, NULL, 3, NULL, 1);
  xTaskCreatePinnedToCore(SensorUpdateTask, "ImulTask", 10000, NULL, 2, NULL, 1);

  command.add('T', ch1doTarget, "ch1 target voltage");
  printf("Cubli_Mini ready. \r\n");
  _delay(1000);
}

void SimpleFocInit()
{
    motor1_i2c.begin(MOTOR_1_SENSOR_I2C_SDA_PIN, MOTOR_1_SENSOR_I2C_SCL_PIN, (uint32_t)400000);
    sensor1.init(&motor1_i2c);
    motor1.linkSensor(&sensor1);
    driver1.voltage_power_supply = 12;
    driver1.init();
    motor1.linkDriver(&driver1);
    motor1.controller = MotionControlType::torque;
    motor1.voltage_limit = 12;
    motor1.useMonitoring(Serial);
    motor1.monitor_downsample = 0;
    motor1.init();
    uint8_t res = motor1.initFOC();
    cubli_mini.SetCh1MotorInitResult(res);
    command.add('M',doMotor,"motor");
}

// core 1
void loop()
{
  motor1.loopFOC();
  motor1.move(cubli_mini.motor_set_speed_.ch1);
  cubli_mini.motor_get_speed_.ch1 = motor1.shaft_velocity;
}

void SerialCmdTask(void *parameter)
{
  for(;;)
  {
#if 0
    command.run();
    motor1.monitor();
#endif
#if USER_SERIAL
    xSemaphoreTake(x_mutex, portMAX_DELAY);
    serial_commander.Run(Serial, cubli_mini.p_balance_.param, cubli_mini.u_ch2_balance_.param);
    if(serial_commander.output_angle_)
    {
        printf("x_A:%f y_A:%f z_A:%f\r\n",
                cubli_mini.p_balance_.sensor.x.angle, 
                cubli_mini.p_balance_.sensor.y.angle,
                cubli_mini.p_balance_.sensor.z.angle);
    }
#if USER_WIFI
    if(wifi_commander.GetConnectStatus() == WifiConnectStatus_e::eWIFI_SUCCESS)
    {
      wifi_commander.sensor_angle_.x = cubli_mini.p_balance_.sensor.x.angle;
      wifi_commander.sensor_angle_.y = cubli_mini.p_balance_.sensor.y.angle;
      wifi_commander.sensor_angle_.z = cubli_mini.p_balance_.sensor.z.angle;
    }
#endif
    xSemaphoreGive(x_mutex);	
#endif 
    _delay(20);
  }
}

void SerialLogTask(void *parameter)
{
    for(;;)
    {
        #if 0
            sensor1.update();
            _delay(1);
            printf("ch1_Angle: %f\r\n", sensor1.getAngle());
        #endif
#if 0
        printf("get speed ch1:%f ch2:%f ch3:%f\r\n", 
        cubli_mini.motor_set_speed_.ch1, 
        cubli_mini.motor_set_speed_.ch2, 
        cubli_mini.motor_set_speed_.ch3);
#endif
#if 0
        printf("angle x:%f y:%f z:%f\r\n", 
        cubli_mini.p_balance_.sensor.x, 
        cubli_mini.p_balance_.sensor.y, 
        cubli_mini.p_balance_.sensor.z);
#endif
        delay(100);
    }
}

#if USER_WIFI
void WifiCommanderTask(void *parameter)
{
  for(;;)
  {
    wifi_commander.TcpTask(cubli_mini.p_balance_.param, cubli_mini.u_ch2_balance_.param);
    delay(2000);
  }
}
#endif

void ModecontrolTask(void *parameter)
{
  for(;;)
  {
    cubli_mini.ModeControl();
    _delay(20);
  }
}

void SensorUpdateTask(void *parameter)
{
  for(;;)
  {
    cubli_mini.SensorUpdate();
    _delay(1);
  }
}

void ControlTask(void *parameter)
{
  for(;;)
  {
    cubli_mini.Control();
    _delay(2);
  }
}

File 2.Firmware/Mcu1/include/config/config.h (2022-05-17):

#pragma once
#include <Arduino.h>

namespace CubliMini {
namespace Config {  

#define USER_WIFI 1
#define USER_SERIAL 1
#define FIRST_DOWNLOAD_CODE 0
#define LOW_POWER_VOLTAGE_THRESHOLD 9.5
#define IMU_INIT_GYRO_THRESHOLD 4
#define IMU_STATIC_GYRO_THRESHOLD 5

#define WIFI_SSID "ChinaNet-RFPPQ9"
#define WIFI_PASSWORD "12345678"

#define WIFI_TCP_SERVER_IP "192.168.2.14"
#define WIFI_TCP_SERVER_PORT 1312

#define MOTOR_PP 7

#define MOTOR_1_PWM1_PIN (int)25
#define MOTOR_1_PWM2_PIN (int)26
#define MOTOR_1_PWM3_PIN (int)27
#define MOTOR_1_EN_PIN (int)33

#define MOTOR_1_SENSOR_I2C_SDA_PIN (int)4
#define MOTOR_1_SENSOR_I2C_SCL_PIN (int)14

#define CAN_TXD_PIN (int)15
#define CAN_RXD_PIN (int)13

#define IMU_SCL_PIN (int)18
#define IMU_SDA_PIN (int)5
#define IMU_INTERRUPT_PIN (int)23

#define BULE_LED_PIN (int)10
#define GREEN_LED_PIN (int)9
#define MOTOR_GREEN_LED_PIN (int)21

#define KEY_1_PIN (int)22
#define KEY_2_PIN (int)19

#define BAT_VOLTAGE_PIN (int)36

} // namespace Cubli 
} // namespace Config 

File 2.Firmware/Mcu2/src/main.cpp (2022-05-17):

#include <Arduino.h>
#include <SimpleFOC.h>
#include <ESP32CAN.h>
#include <CAN_config.h>
#include "config/config.h"
#include "bsp/bsp_driver.h"
#include "comm/type.h"

using namespace Cubli::Comm;
using namespace Cubli::Bsp;
using namespace Cubli::Config;

MotorControl_t motor_control;
DeviceStatus_t device_status;

BspDriver bsp_driver;
MagneticSensorI2C sensor2 = MagneticSensorI2C(AS5600_I2C);
TwoWire i2c2 = TwoWire(0);
MagneticSensorI2C sensor3 = MagneticSensorI2C(AS5600_I2C);
TwoWire i2c3 = TwoWire(1);

BLDCMotor motor2 = BLDCMotor(MOTOR_2_PP);
BLDCMotor motor3 = BLDCMotor(MOTOR_3_PP);

BLDCDriver3PWM driver2 = BLDCDriver3PWM(MOTOR_2_PWM1_PIN, MOTOR_2_PWM2_PIN, MOTOR_2_PWM3_PIN, MOTOR_2_EN_PIN);
BLDCDriver3PWM driver3 = BLDCDriver3PWM(MOTOR_3_PWM1_PIN, MOTOR_3_PWM2_PIN, MOTOR_3_PWM3_PIN, MOTOR_3_EN_PIN);

void CanTask(void *parameter);
void LedTask(void *parameter);
void SimpleFocInit();

void setup()
{
  Serial.begin(115200);

  memset(&motor_control, 0, sizeof(motor_control));
  memset(&device_status, 0, sizeof(device_status));

  bsp_driver.Init();
  SimpleFocInit();

  xTaskCreatePinnedToCore(CanTask, "can tx task", 10000, NULL, 2, NULL, 1);
  xTaskCreatePinnedToCore(LedTask, "led task", 10000, NULL, 3, NULL, 1);

  printf("Motor ready.");
  _delay(1000);
}

void SimpleFocInit()
{
  i2c2.begin(MOTOR_2_SENSOR_I2C_SDA_PIN, MOTOR_2_SENSOR_I2C_SCL_PIN, (uint32_t)400000);
  sensor2.init(&i2c2);

  i2c3.begin(MOTOR_3_SENSOR_I2C_SDA_PIN, MOTOR_3_SENSOR_I2C_SCL_PIN, (uint32_t)400000);
  sensor3.init(&i2c3);

  motor2.linkSensor(&sensor2);
  motor3.linkSensor(&sensor3);

  driver2.voltage_power_supply = 12;
  driver2.init();
  motor2.linkDriver(&driver2);

  driver3.voltage_power_supply = 12;
  driver3.init();
  motor3.linkDriver(&driver3);

  motor2.controller = MotionControlType::torque;
  motor3.controller = MotionControlType::torque;
  motor2.voltage_limit = 12;
  motor3.voltage_limit = 12;

  motor2.useMonitoring(Serial);
  motor3.useMonitoring(Serial);

  motor2.init();
  if (motor2.initFOC() == Result_e::eSUCCESS)
  {
    device_status.ch2_motor_init_result = Result_e::eSUCCESS;
  }
  else
  {
    device_status.ch2_motor_init_result = Result_e::eFail;
  }

  motor3.init();
  if (motor3.initFOC() == Result_e::eSUCCESS)
  {
    device_status.ch3_motor_init_result = Result_e::eSUCCESS;
  }
  else
  {
    device_status.ch3_motor_init_result = Result_e::eFail;
  }
}

void CanTask(void *parameter)
{
  for (;;)
  {
    bsp_driver.can_.CanSendMotorSpeed(motor_control.send_speed.ch2_speed, motor_control.send_speed.ch3_speed);
    bsp_driver.can_.CanGetMotorSpeed(motor_control.set_speed.ch2_speed, motor_control.set_speed.ch3_speed);
    device_status.can_status = bsp_driver.can_.CanIsOnline();
    if (device_status.can_status == CanStatus_e::eOFF_LINE)
    {
        motor_control.set_speed.ch2_speed = motor_control.set_speed.ch3_speed = 0;
    }
    _delay(2);
  }
}

// LED指示灯优先级, 电机状态 > CAN掉线 > 正常
// bit 2: bit 1: bit 0
//   can   ch3    ch2
void LedTask(void *parameter)
{
  for (;;)
  {
    uint8_t status = (uint8_t)device_status.can_status << 2 | (uint8_t)device_status.ch3_motor_init_result << 1 | (uint8_t)device_status.ch2_motor_init_result;
    switch (status)
    {
    // 所有设备正常
    case 0x07:
      bsp_driver.motor_green_led_.Control(200, 1, 3000);
      break;
    // 设备有问题
    default:
      bsp_driver.motor_green_led_.Control(200, 3, 3000);
    }
    _delay(100);
  }
}

void loop()
{
  motor2.loopFOC();
  motor3.loopFOC();
  motor2.move(motor_control.set_speed.ch2_speed);
  motor3.move(motor_control.set_speed.ch3_speed);

  motor_control.send_speed.ch2_speed = motor2.shaft_velocity;
  motor_control.send_speed.ch3_speed = motor3.shaft_velocity;
// read sensor value
#if 0
    sensor2.update();
    sensor3.update();
     _delay(1);
    printf("ch1_Angle: %f, ch2_Angle: %f \r\n", sensor2.getAngle(), sensor3.getAngle());
    printf(" speed1: %d, speed2: %d \r\n", sensor2.getVelocity(), sensor3.getVelocity());
#endif
}

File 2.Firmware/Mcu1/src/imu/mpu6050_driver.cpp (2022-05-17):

#include "imu/mpu6050_driver.h"

namespace CubliMini {
namespace ImuDriver {  

bool interrupt_flag = false;

void ARDUINO_ISR_ATTR InterruptFuntion()
{
  interrupt_flag = true;
}

bool Mpu6050Driver::GetMPU6050InterruptFlag()
{
  interrupt_flag_ = interrupt_flag;
  return interrupt_flag_;
}

void Mpu6050Driver::ResetMPU6050InterruptFlag()
{
    interrupt_flag = interrupt_flag_ = false;
}

void Mpu6050Driver::MPU6050InterruptInit()
{
    pinMode(interrupt_pin_, INPUT_PULLUP);
    attachInterrupt(interrupt_pin_, InterruptFuntion, FALLING);
}

bool Mpu6050Driver::Init(TwoWire* _wire, int _sda_pin, int _scl_pin, int _interrupt_pin)
{
    i2c_ = _wire;
    i2c_->begin(_sda_pin, _scl_pin, (uint32_t)400000);
    interrupt_pin_ = _interrupt_pin;
    SetAccRange(AccConfig_e::eACCEL_4G);
    SetGyroRange(GyroConfig_e::eGYRO_1000DEGS);
    if(MPU6050Init() == true)
    {
        printf("IMU: init successful!!!\r\n");
    }
    else
    {
        printf("IMU: init fail!!!\r\n");
    }
    MPU6050InterruptInit();
    delay(100);
    CalGyroOffset();
    return true;
}

void Mpu6050Driver::ImuGetRtValue(ImuData_t &_imu_data, ImuRawData_t &_imu_raw_data)
{
    MPU6050ReadData(_imu_raw_data, _imu_data);
}

void Mpu6050Driver::SetAccRange(const AccConfig_e &_acc_config)
{
    acc_config_ = _acc_config;
    switch(acc_config_)
    {
        case eACCEL_2G: 
            acc_range_ = 2;
            break;
        case eACCEL_4G: 
            acc_range_ = 4;
            break;
        case eACCEL_8G: 
            acc_range_ = 8;
            break;
        case eACCEL_16G: 
            acc_range_ = 16;
            break;
        default:
            acc_range_ = 2;
            acc_config_ = eACCEL_2G;
            break;
    }
}

void Mpu6050Driver::SetGyroRange(const GyroConfig_e &_gyro_config)
{
    gyro_config_ = _gyro_config;
    switch(gyro_config_)
    {
        case eGYRO_250DEGS: 
            gyro_range_ = 250;
            break;
        case eGYRO_500DEGS: 
            gyro_range_ = 500;
            break;
        case eGYRO_1000DEGS: 
            gyro_range_ = 1000;
            break;
        case eGYRO_2000DEGS: 
            gyro_range_ = 2000;
            break;
        default:
            gyro_range_ = 1000;
            gyro_config_ = eGYRO_1000DEGS;
            break;
    }
}

bool Mpu6050Driver::MPU6050Init()
{
  if (uint8_t _id = GetMPU6050Id() != MPU6050_DEVICE_ID)
  {
    printf("IMU: can not find mpu6050, get id: \r\n", _id);
    return false;
  }

  if (I2cWrite(MPU6050_I2CADDR_DEFAULT, MPU6050_PWR_MGMT_1, 0x01) != ESP_OK) // 解除休眠模式
  {
    printf("IMU: 0x01 \r\n");
    return false;
  }

  if (I2cWrite(MPU6050_I2CADDR_DEFAULT, MPU6050_CONFIG, DLPFConfig_e::eDLPF_94HZ) != ESP_OK)
  {
    printf("IMU: 0x02 \r\n");
    return false;
  }

  if (I2cWrite(MPU6050_I2CADDR_DEFAULT, MPU6050_GYRO_CONFIG, gyro_config_) != ESP_OK)
  {
    printf("IMU: 0x03 \r\n");
    return false;
  }

  if (I2cWrite(MPU6050_I2CADDR_DEFAULT, MPU6050_ACCEL_CONFIG, acc_config_) != ESP_OK)
  {
    printf("IMU: 0x04 \r\n");
    return false;
  }

  if (I2cWrite(MPU6050_I2CADDR_DEFAULT, MPU6050_INT_PIN_CONFIG, 0x02) != ESP_OK) // logic level for the INT pin is active high
  {
    printf("IMU: 0x05 \r\n");
    return false;
  }

  if (I2cWrite(MPU6050_I2CADDR_DEFAULT, MPU6050_INT_ENABLE, 0x01) != ESP_OK) // able data ready interrupt
  {
    printf("IMU: 0x06 \r\n");
    return false;
  }

  if (I2cWrite(MPU6050_I2CADDR_DEFAULT, MPU6050_SMPLRT_DIV, 0x00) != ESP_OK) // Sample Rate: Gyro output rate / (1 + 0) = 1000Hz
  {
    printf("IMU: 0x07 \r\n");
    return false;
  }

  delay(100);

  imu_init_seccessfully_ = true;
  return true;
}


uint8_t Mpu6050Driver::GetMPU6050Id()
{
  uint8_t _id;
  I2cRead(MPU6050_I2CADDR_DEFAULT, MPU6050_WHO_AM_I, &_id, 1);
  return _id;
}

uint8_t Mpu6050Driver::I2cWrite(int _address, int _res, int _data)
{
  i2c_->beginTransmission(_address);
  i2c_->write(_res);
  i2c_->write(_data);
  return i2c_->endTransmission();
}

uint8_t Mpu6050Driver::I2cRead(int _address, int _res, uint8_t *_buff, int _size)
{
  i2c_->beginTransmission(_address);
  i2c_->write(_res);
  i2c_->endTransmission();
  // read data
  uint8_t read_len = i2c_->requestFrom(_address, _size);
  for (byte i = 0; i < read_len; ++i)
  {
    _buff[i] = i2c_->read();
  }
  return read_len;
}

void Mpu6050Driver::MPU6050ReadData(ImuRawData_t & _imu_raw_data, ImuData_t & _imu_data)
{
  uint8_t mpu_buf[14] = { 0 };

  I2cRead(MPU6050_I2CADDR_DEFAULT, MPU6050_ACCEL_OUT, mpu_buf, 14);
  _imu_raw_data.acc.ax = (((int16_t)mpu_buf[0]) << 8) | mpu_buf[1];   // ax
  _imu_raw_data.acc.ay = (((int16_t)mpu_buf[2]) << 8) | mpu_buf[3];   // ay
  _imu_raw_data.acc.az = (((int16_t)mpu_buf[4]) << 8) | mpu_buf[5];   // az

  _imu_raw_data.temp = (((int16_t)mpu_buf[6]) << 8) | mpu_buf[7];   // temp

  _imu_raw_data.gyro.gx = (((int16_t)mpu_buf[8]) << 8) | mpu_buf[9];   // gx
  _imu_raw_data.gyro.gy = (((int16_t)mpu_buf[10]) << 8) | mpu_buf[11]; // gy
  _imu_raw_data.gyro.gz = (((int16_t)mpu_buf[12]) << 8) | mpu_buf[13]; // gz

  MeanFilter(_imu_raw_data);

  _imu_raw_data = mean_imu_raw_data_;

  // 转为g
  _imu_data.acc.ax = (float)_imu_raw_data.acc.ax / (32768 / acc_range_); 
  _imu_data.acc.ay = (float)_imu_raw_data.acc.ay / (32768 / acc_range_); 
  _imu_data.acc.az = (float)_imu_raw_data.acc.az / (32768 / acc_range_); 

  // 转成度每秒
  _imu_data.gyro.gx = (float)_imu_raw_data.gyro.gx / (32768 / gyro_range_) - gyro_offset_.gx; 
  _imu_data.gyro.gy = (float)_imu_raw_data.gyro.gy / (32768 / gyro_range_) - gyro_offset_.gy; 
  _imu_data.gyro.gz = (float)_imu_raw_data.gyro.gz / (32768 / gyro_range_) - gyro_offset_.gz; 
  _imu_data.temp = 36.53f + (float)_imu_raw_data.temp / 340;
}
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

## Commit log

2022-05-18 修复动量轮漏倒角问题，添加了采购的注意事项
    [YC.JGJ.000002.4.DWG, YC.JGJ.000002.DWG]
2022-05-21 添加3D打印件和钣金件的step文件，readme备注文件修改，添加安全说明
    [YC.JGJ.000001.STEP, YC.JGJ.000002.4.STEP, YC.JGJ.000003.STEP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]
2022-05-22 给PCB的BOM表添加链接，文档更加详细的说明如何解决头文件问题
    [AS5600.xlsx, Cubli_Control_Board.xlsx, ESP32_UART.xlsx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]
2022-06-09 修复: 修复了PCB BOM几处链接错误问题
    [AS5600.xlsx, Cubli_Control_Board.xlsx, ESP32_UART.xlsx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]
